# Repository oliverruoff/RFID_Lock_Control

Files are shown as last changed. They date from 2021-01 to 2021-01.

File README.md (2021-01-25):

# RFID_Lock_Control

A small system, used to turn a key, based on RFID authorization.

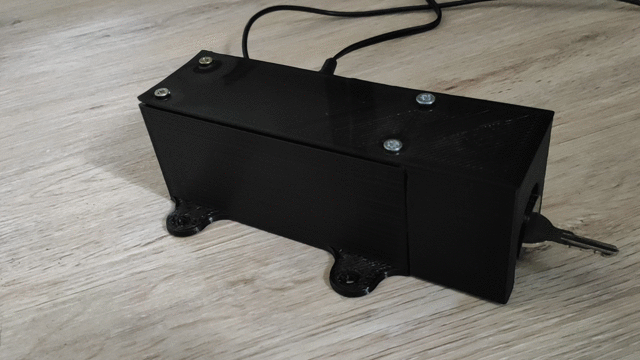
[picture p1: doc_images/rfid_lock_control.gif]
RFID Lock Control

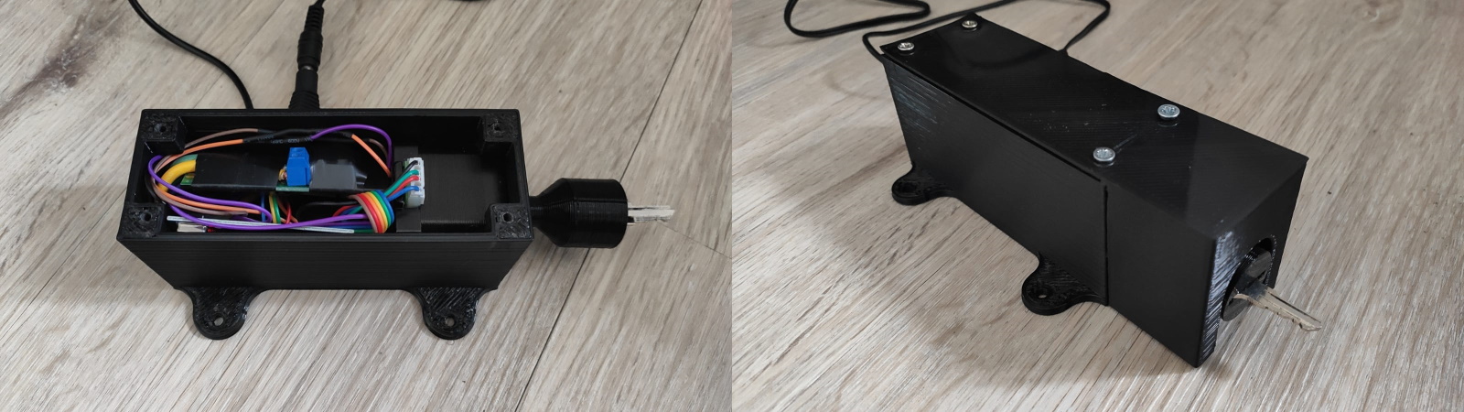
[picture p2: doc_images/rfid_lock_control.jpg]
RFID Lock Control

> For more pictures / gifs, check the [Illustration](#Illustration) section.

## Hardware used

This is a list of the main parts (not including required wires etc.)

- Raspberry Pi Zero W
- Stepper Motor ( 12V 1.5A )
- 12V Power Supply
- Motor Driver ( UEETEK **DRV8825** )
- RFID Writer / Reader ( AZDelivery RFID kit RC522 (including RFID chip))
- 3D printed parts (see [stls folder](./stls))

## Wiring

### Stepper Wiring

> Note that I connected the `RST` and `SLP` pins of the motor driver not to the 3.3V pin (as shown on the wiring image), but to a GPIO pin that can be set to LOW, in order to be able to deactivate the stepper motor when not used (remove holding torque), to save energy. When you want to turn the stepper motor, raise this pin to HIGH. (Of course, you can also simply connect `RST` and `SLP` to a 3.3V pin (as shown on the wiring image) if you don't want to save energy while the motor is not turning (or want holding torque)).

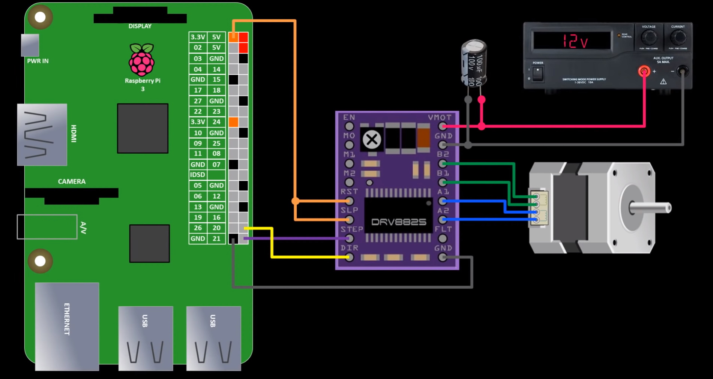
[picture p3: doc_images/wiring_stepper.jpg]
wiring


### RFID Wiring

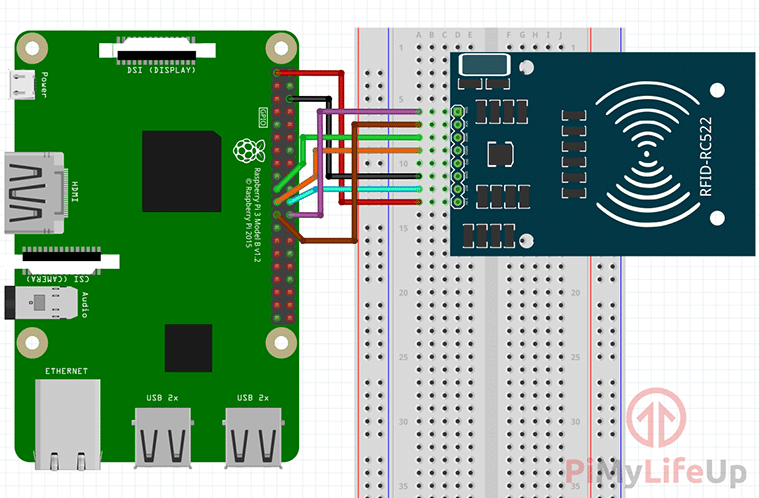
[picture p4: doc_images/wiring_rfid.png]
wiring


## Stepper

To connect the stepper motor to the driver and raspberry, refer to this [youtube video](https://www.youtube.com/watch?v=LUbhPKBL_IU&t=258s).  
Don't miss to adjust the motor driver, so you don't fry your motor. (set current to max. 71% of max. motor current, in this case 1.5Ah --> driver current max. 1.065A (0.71 x 1.5). You should be fine with ~0.7A).

## RFID

To setup the RFID module, refer to [this guide](https://pimylifeup.com/raspberry-pi-rfid-rc522/)  
  
**tldr**:

- sudo raspi-config -> interfacing options -> activate spi interface
- reboot
- sudo nano /boot/config.txt --> uncomment (or if not exist, add) the line `dtparam=spi=on`
- sudo apt-get update
- sudo apt-get upgrade
- sudo pip3 install spidev
- sudo pip3 install mfrc522

## Usage

In the file [.registered_uids](./code/.registered_uids), the uids are listed (split by newlines), that are allowed to open the lock.  
If no uids are registered yet, the program will directly enter the learning mode, to register the first uid. **The first listed uid, also works as master key.**  
There are two things you can do with the master key:
1. Register new uids (RFID chips):
    - Therefore, simply scan the master card, the motor will do some short movements to show that the system is in learning mode. Now scan the RFID chip, you want the system to register. After that, the system will do some movements to show it worked (or different movements if not)and continue with its unlock routine.
2. Unlock the system:
    - Therefore, simply scan the master card, the motor will do some short movements to show that the system is in learning mode. Now simply rescan the master card. The system will notice, that this uid is already registered, will stop the learning mode and do its unlock routine.

All other registered uids in [.registered_uids](./code/.registered_uids) (line 2 and on), are only allowed to unlock the system, not to register new uids.  
Uids that are not registered (not saved to [.registered_uids](./code/.registered_uids)) won't be able to unlock the system and the system will show that by doing five short movements.  

## Setting things up for autostart on linux systems as service (developed for Raspberry Pi)

* Install python3
* Checkout this repository on raspberry pi
* Install modules listed in `requirements.txt`
* Make `main.py` executable
    * $ `chmod +x main.py`
* Copy `rlc.service` to `/lib/systemd/system`
* Change `ExecStart=` command inside `rlc.service` accordingly to the path where `main.py` is located (incl. 'main.py' at the end)
* Change `WorkingDirectory=` command inside `rlc.service` accordingly to the path where `main.py` is located (ending with the 'code' folder)
* Enable daemon process
    * $ `sudo systemctl daemon-reload`
    * $ `sudo systemctl enable rlc.service`
    * $ `sudo systemctl start rlc.service`
* Enable daily reboot at midnight (to automatically fix (e.g.) networking errors
  * `sudo crontab -e`
  * Enter as new line and save --> `0 0 * * * /sbin/reboot`

## Useful commands for process monitoring

* Check status
    * $ `sudo systemctl status rlc.service`
* Start service
    * $ `sudo systemctl start rlc.service`
* Stop service
    * $ `sudo systemctl stop rlc.service`
* Check service's log
    * $ `sudo journalctl -f -u rlc.service`

## Illustration

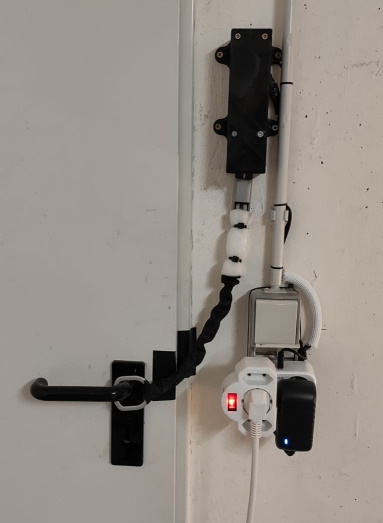
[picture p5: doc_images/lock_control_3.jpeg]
RFID Lock Control

RFID Lock Control
RFID Lock Control

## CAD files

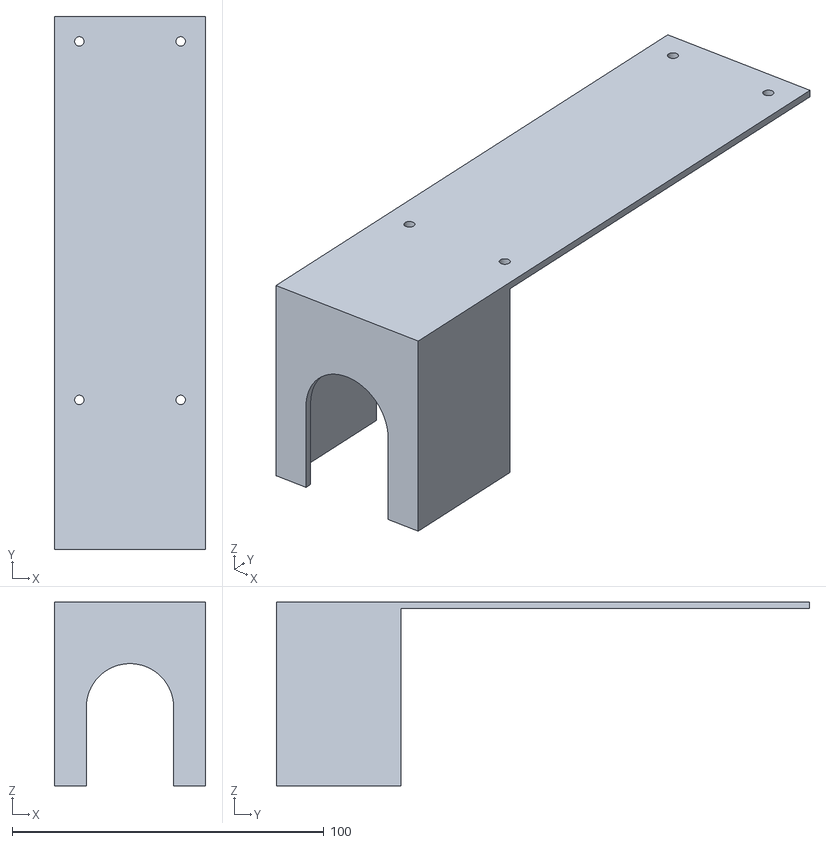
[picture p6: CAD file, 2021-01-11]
stls/Basement_NFC_Key_Top.stl
48.5 x 171.0 x 59.0

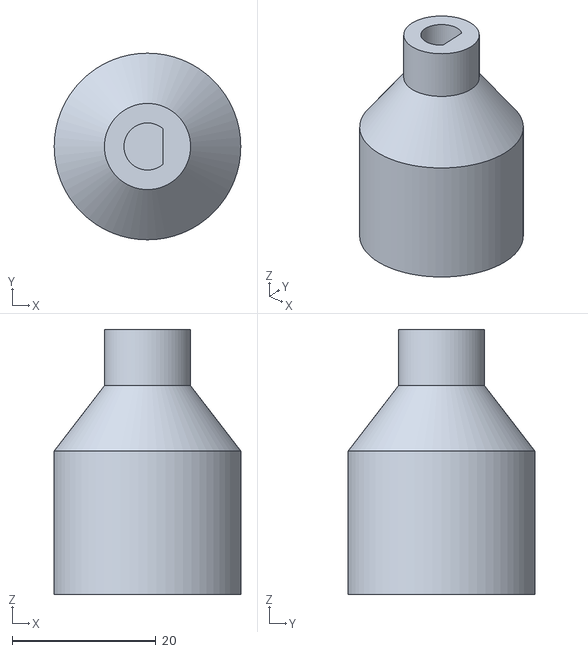
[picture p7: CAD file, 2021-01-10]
stls/RFID_Lock_Control_Key_Adaptor.stl
26.0 x 26.0 x 36.9

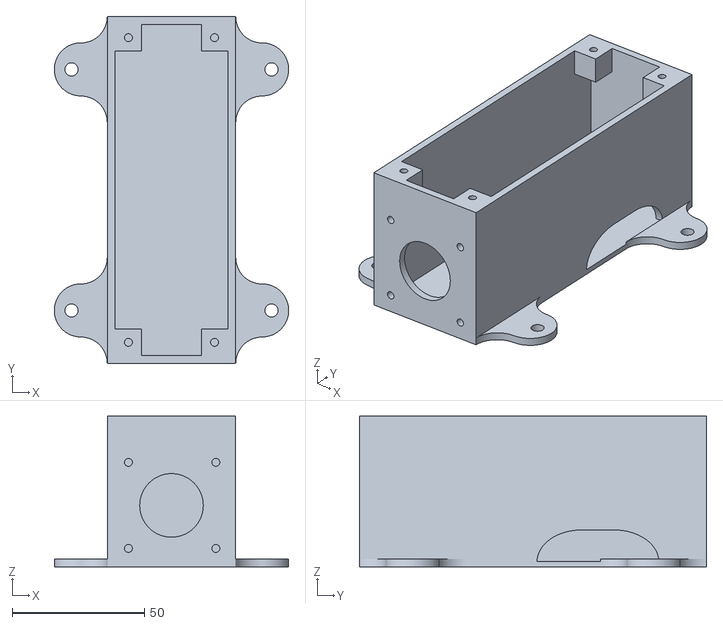
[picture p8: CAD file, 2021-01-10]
stls/RFID_Lock_Control_Case.stl
88.5 x 131.0 x 57.0

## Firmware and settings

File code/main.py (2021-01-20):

#!/usr/bin/env python

import RPi.GPIO as GPIO

import stepper
import rfid
import inout

REGISTERED_UIDS_FILE = '.registered_uids'
LOG_FILE = 'log.txt'


def save_new_uid(uid):
    inout.write_log_file(LOG_FILE, 'Registered new uid:', uid)
    inout.append_text_line_to_file(REGISTERED_UIDS_FILE, uid)
    registered_uids.append(uid)
    print('Successfully registered new uid:', uid)


def register_first_key_as_master(uid):
    stepper.toggle_stepper(20, 1, 0.2)
    save_new_uid(uid)
    stepper.toggle_stepper(20, 2, 0.2)


def register_new_uid():
    stepper.toggle_stepper(20, 1, 0.2)
    uid, _ = rfid.read_rfid()
    if uid not in registered_uids:
        save_new_uid(uid)
    else:
        print('Uid is already registered!')
    stepper.toggle_stepper(20, 2, 0.2)


if __name__ == "__main__":
    try:
        registered_uids = inout.read_lines_from_file(REGISTERED_UIDS_FILE)
        print('Registered uids:', registered_uids)
        while True:
            print('Listening to RFID module...')
            uid, text = rfid.read_rfid()
            print(uid, uid in registered_uids)
            # First time using the lock control -> registering master key
            if len(registered_uids) == 0:
                print('No uids registered yet, registering new (master) key.')
                register_first_key_as_master(uid)
            # Master key recognized
            elif uid == registered_uids[0]:
                print('Master key recognized! Registering new uid...')
                register_new_uid()
            # Registered key recognized
            if uid in registered_uids:
                print('Unlocked!')
                inout.write_log_file(LOG_FILE, 'Opened lock with uid:', uid)
                stepper.toggle_stepper(110, 1, 0.5)
            # Unregistered key recognized
            else:
                print('Unauthorized! Sorry :P')
                inout.write_log_file(
                    LOG_FILE, 'Refused to open lock with uid:', uid)
                stepper.toggle_stepper(5, 5, 0.2)

    except KeyboardInterrupt:
        pass
    finally:
        GPIO.cleanup()

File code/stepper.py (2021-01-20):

from time import sleep
import RPi.GPIO as GPIO

DIR = 20   # Direction GPIO Pin
STEP = 21  # Step GPIO Pin
CW = 1     # Clockwise Rotation
CCW = 0    # Counterclockwise Rotation
SPR = 200   # Steps per Revolution (360 / 1.8) (1,8° per step (oruoff))
STEPPER_ACTIVATION_PIN = 4  # If set to Low, there is no holding torque on the motor


GPIO.setmode(GPIO.BCM)
GPIO.setup(DIR, GPIO.OUT)
GPIO.setup(STEP, GPIO.OUT)
GPIO.setup(STEPPER_ACTIVATION_PIN, GPIO.OUT)

GPIO.output(DIR, CW)
delay = .0005


def turn_stepper(degree, clockwise=True):
    GPIO.output(STEPPER_ACTIVATION_PIN, GPIO.HIGH)
    direction = CCW
    if clockwise:
        direction = CW
    GPIO.output(DIR, direction)
    for _ in range(int(SPR/360*degree)):
        GPIO.output(STEP, GPIO.HIGH)
        sleep(delay)
        GPIO.output(STEP, GPIO.LOW)
        sleep(delay)
    GPIO.output(STEPPER_ACTIVATION_PIN, GPIO.LOW)


def toggle_stepper(degree, repetitions, delay, start_clockwise=True):
    clockwise = start_clockwise
    for _ in range(repetitions):
        for __ in range(2):
            turn_stepper(degree, clockwise)
            clockwise = False if clockwise else True
            sleep(delay)

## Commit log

2021-01-10 Improved README.md
    [RFID_Lock_Control_Case.stl, RFID_Lock_Control_Key_Adaptor.stl, RFID_Lock_Control_Key_Hide.stl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]
2021-01-11 Added logs, fixed registering new uid
    [main.py]
2021-01-11 Fix all log datetimes
    [main.py]
2021-01-11 Updated .stl files
    [Basement_NFC_Key_Top.stl, RFID_Lock_Control_Key_Hide.stl, RFID_Lock_Control_Top.stl]
2021-01-12 smoothened stepper movement
